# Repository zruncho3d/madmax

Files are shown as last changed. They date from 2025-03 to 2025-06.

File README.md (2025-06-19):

## MadMax - the crazy-simple toolchanger *conversion* for your CoreXY printer

Enable multi-material printing *on the printer you already own* - with low cost, low effort, low filament waste, and fast multi-material switching.
<br><br>

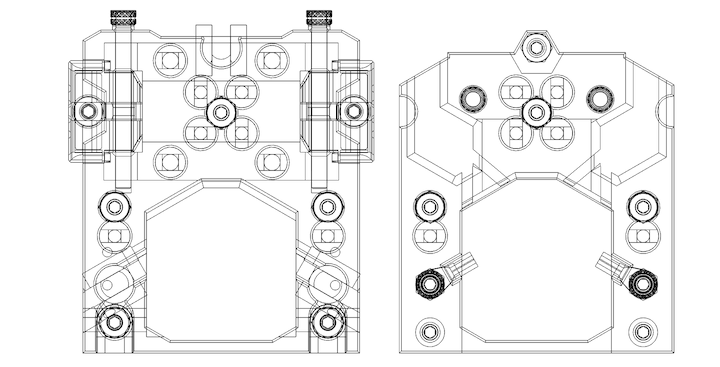
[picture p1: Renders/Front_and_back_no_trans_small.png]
 |  | gif | gif |
| --- | --- | --- |
| Solid Core<br>new plate + carriage design using Maxwell coupling | Fast Toolchanging<br>(`Yell`'s E3-to-Trident with AntHeads)  | Quality Printing<br> (`Andrewmcgr`'s VT 350 with A4Ts) |

<br><br>
**MadMax is currently in active beta**, with over 12+ completed builds doing two-head printing:
<br><br>

| Printer | Image | Sample | Description |
| --- | ---- | ---- | ---- |
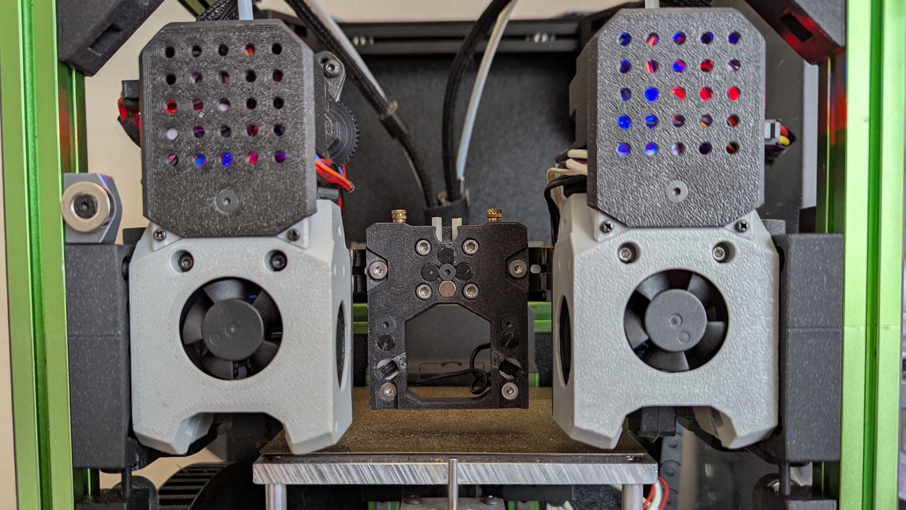
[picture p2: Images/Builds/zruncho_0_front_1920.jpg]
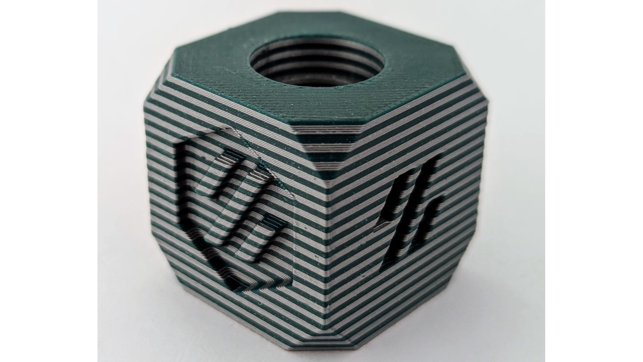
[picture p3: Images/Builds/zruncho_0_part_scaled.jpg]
| Zruncho's T0 120 (MM.000)|  |   | T0+B0, Vampire Bat, Nudge, custom rear-shift bed parts, OmniBrick heads, PapLite belt extruders, docks + brushes/blockers by Zruncho.|
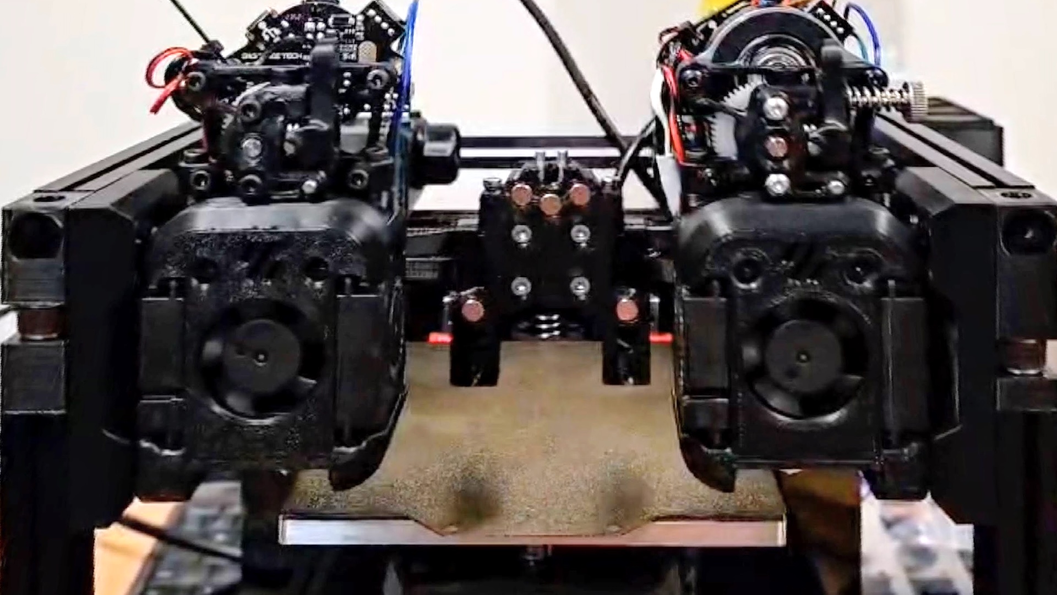
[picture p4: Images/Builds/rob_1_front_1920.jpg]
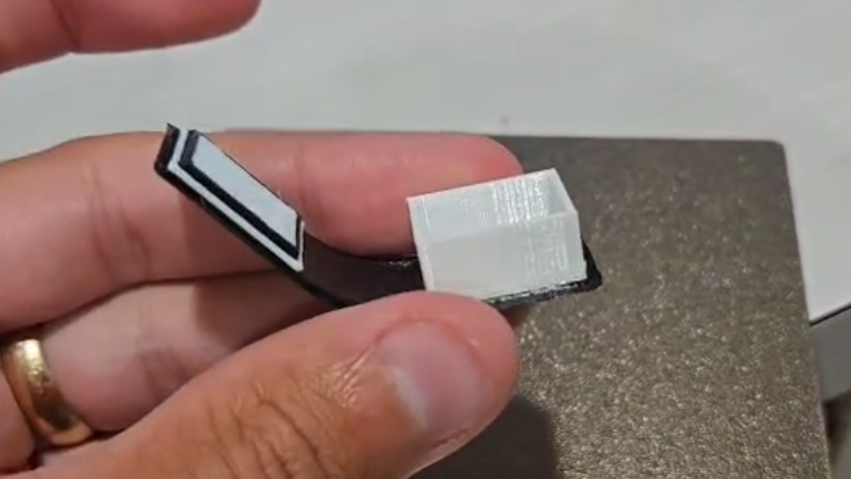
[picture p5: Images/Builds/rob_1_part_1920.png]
| Rob's V0 120 (MM.001) |  |  | Voron Zero, Vampire Bat, DragonBricks, V0 docks by Rob, Custom K1 extruders by Rob.|
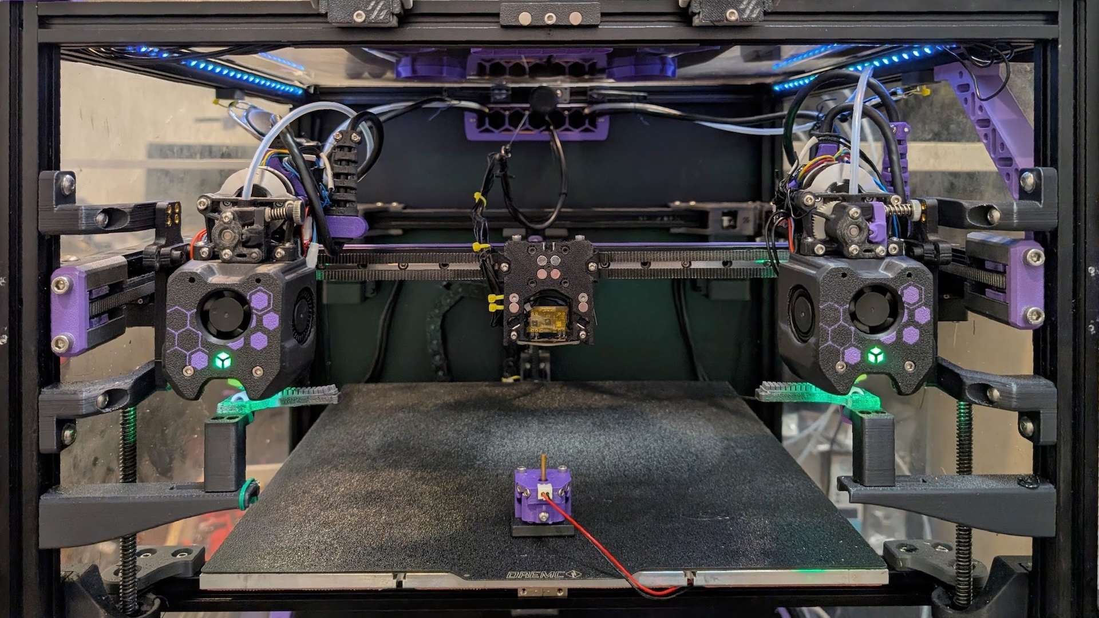
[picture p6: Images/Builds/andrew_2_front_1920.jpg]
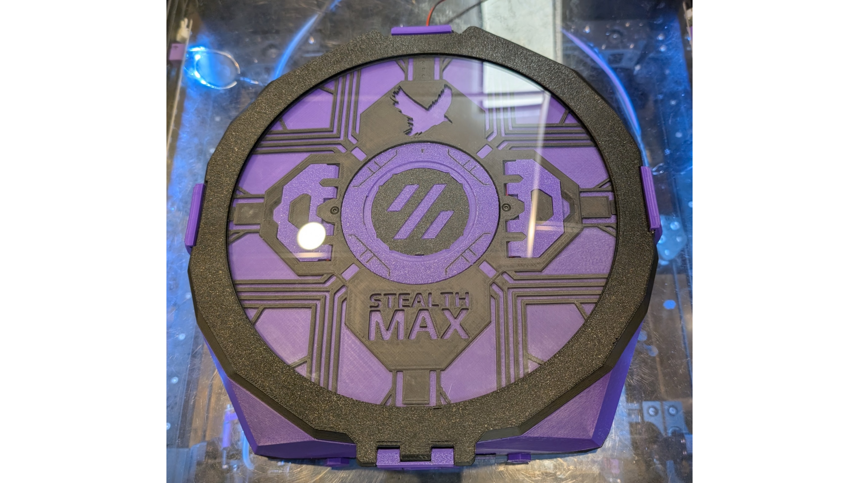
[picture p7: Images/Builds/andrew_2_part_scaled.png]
| andrewmcgr's VT 350 (MM.002) |  |  | Trident 350, A4Ts, Sherpa Minis, TMC 4671 closed-loop servo XY drives, BFI, Cartographer. Docks, brushes, carriage, plate by Andrew.|
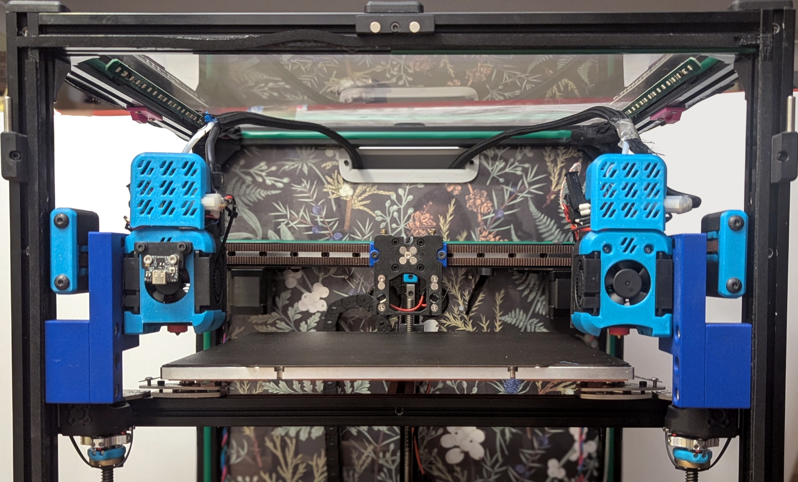
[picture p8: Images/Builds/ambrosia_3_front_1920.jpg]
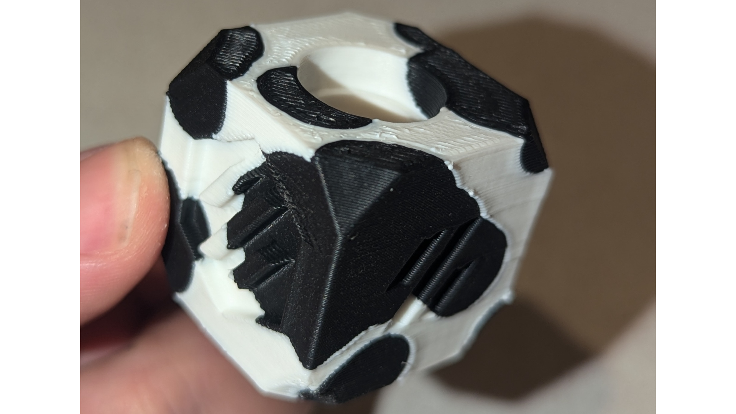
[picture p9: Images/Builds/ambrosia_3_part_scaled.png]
| Ambrosia's Metal VT (MM.003) |  |  | Metal Trident with DragonBricks, Trident stalagmite docks by Ambrosia, as seen on [Canuck Creator](https://www.youtube.com/watch?v=dB9FqNF6or0&t=164s)! |
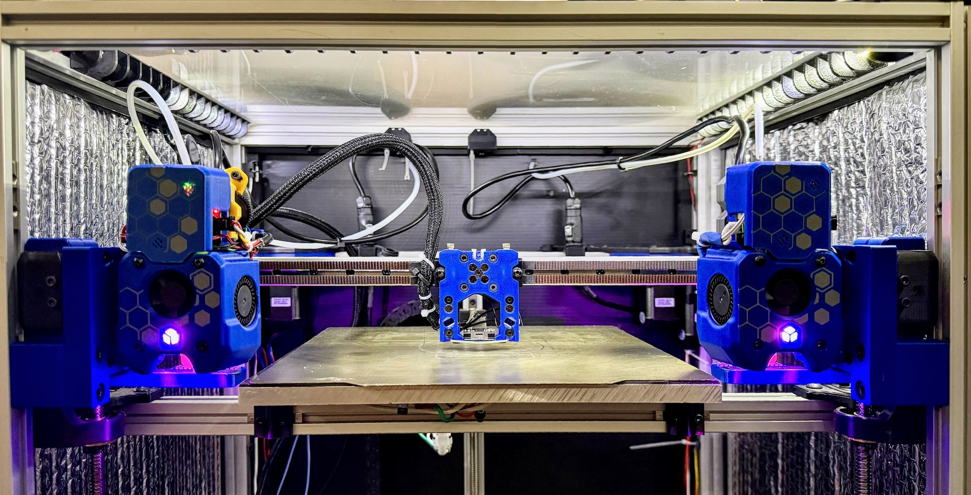
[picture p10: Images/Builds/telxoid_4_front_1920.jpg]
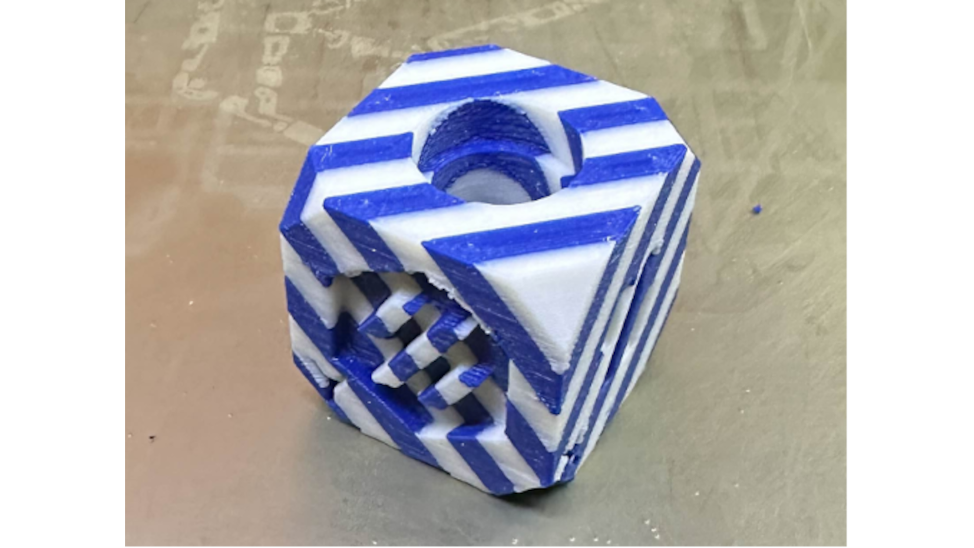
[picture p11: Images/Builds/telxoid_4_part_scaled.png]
| Telxoid's Tridex 250 (350 wide) (MM.004) |   |  | Tridex, A4TBrick, PapLite belt extruders, docks + brushes/blockers by Telxoid.  Running y-assist CoreXY!
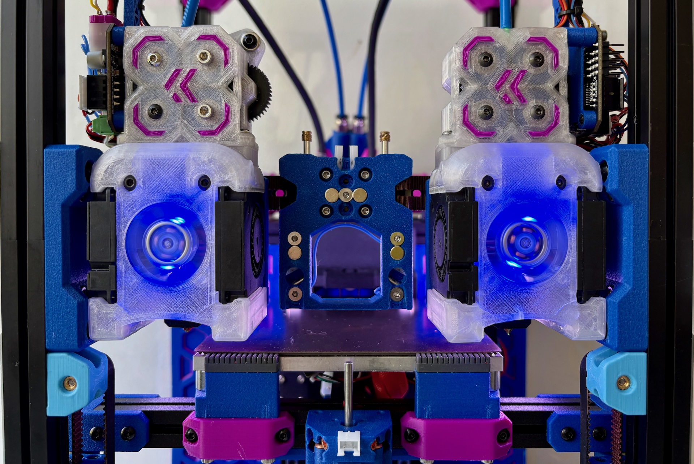
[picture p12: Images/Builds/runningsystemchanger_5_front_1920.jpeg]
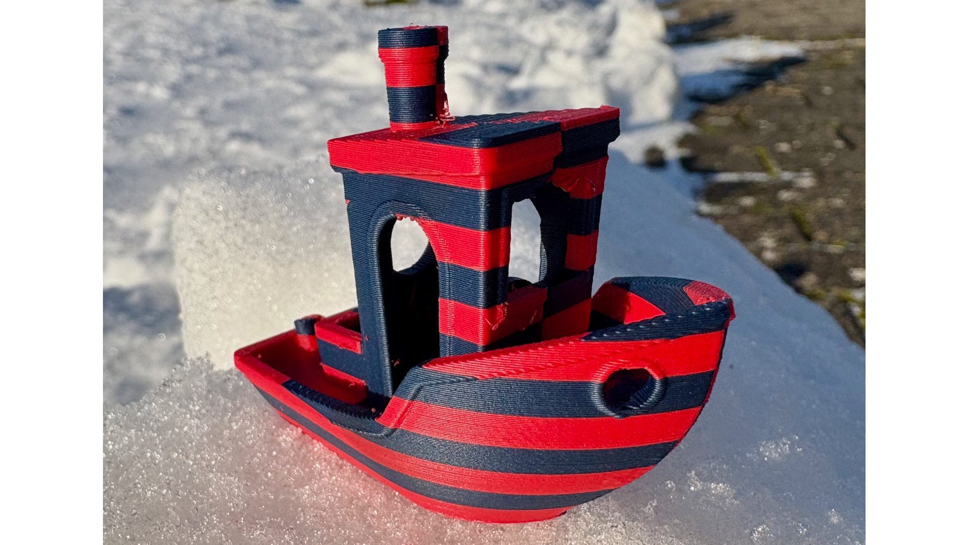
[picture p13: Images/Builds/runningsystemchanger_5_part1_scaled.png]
| Max's HX0 120 (MM.005) |  |  | HX0+B0, VB, DBs, custom PapLite Slim mount, side-mount TH board, Y-shift HammerHead bed by Max.|
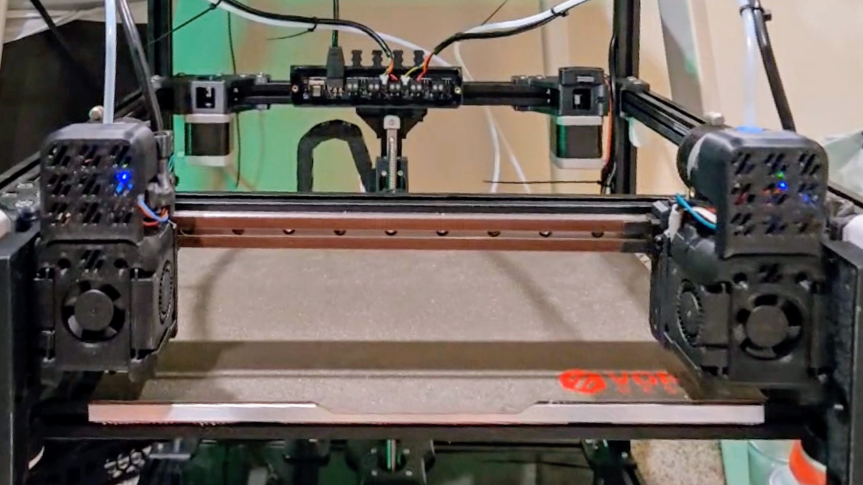
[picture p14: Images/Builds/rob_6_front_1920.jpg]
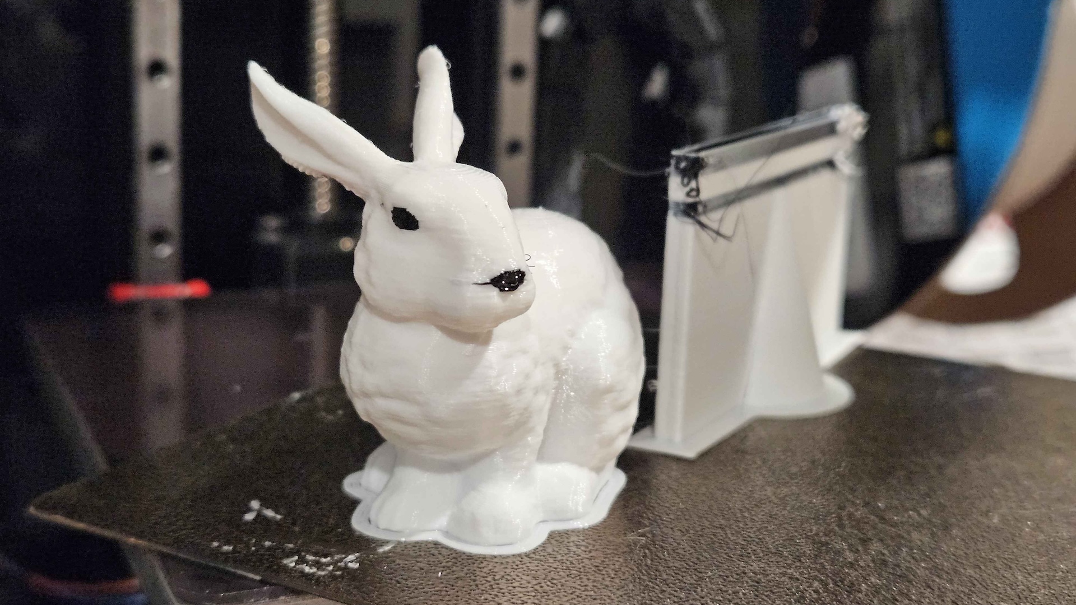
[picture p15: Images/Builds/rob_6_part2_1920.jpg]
| Rob's VT (MM.006) |  |  | RapidBrick heads by Rob, Trident stalagmite docks by Ambrosia.|
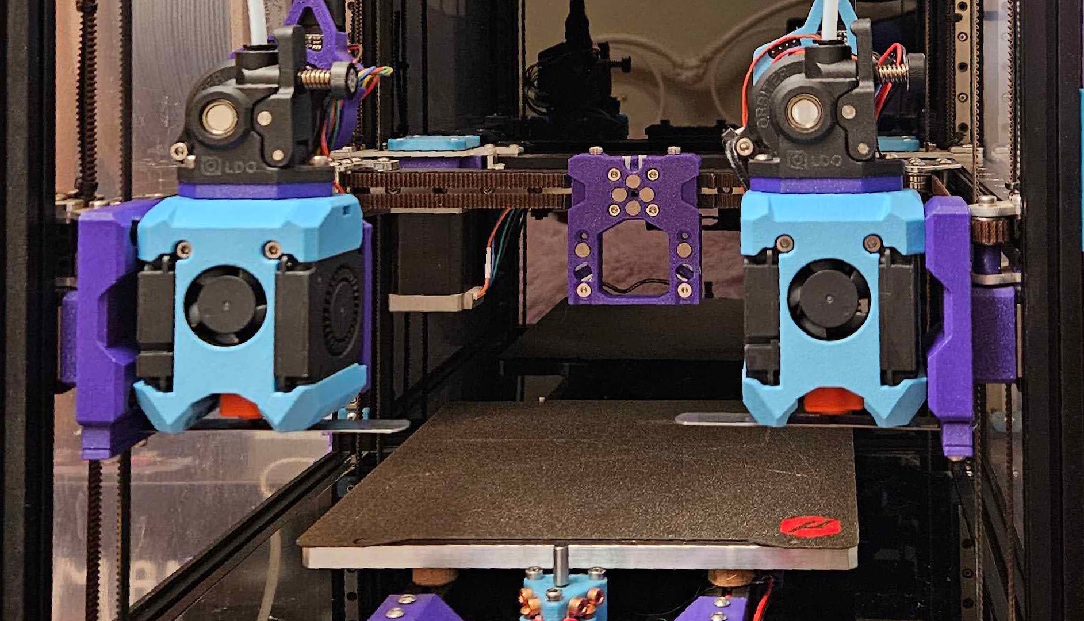
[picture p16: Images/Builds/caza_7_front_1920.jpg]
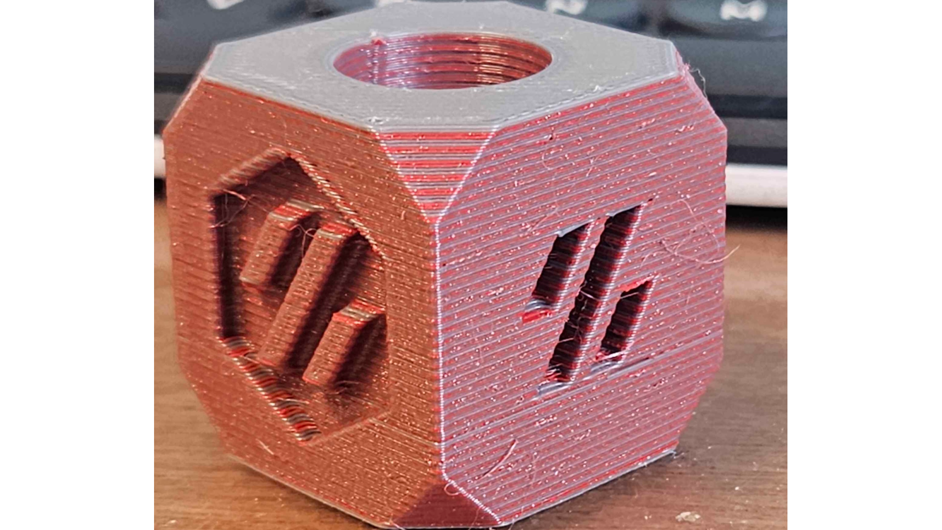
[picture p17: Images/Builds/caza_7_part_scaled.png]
| Caza's Metal Micron (MM.007) |  |   |  Yavoth heads by Caza, Orbiter extruders, Micron Docks by Caza.
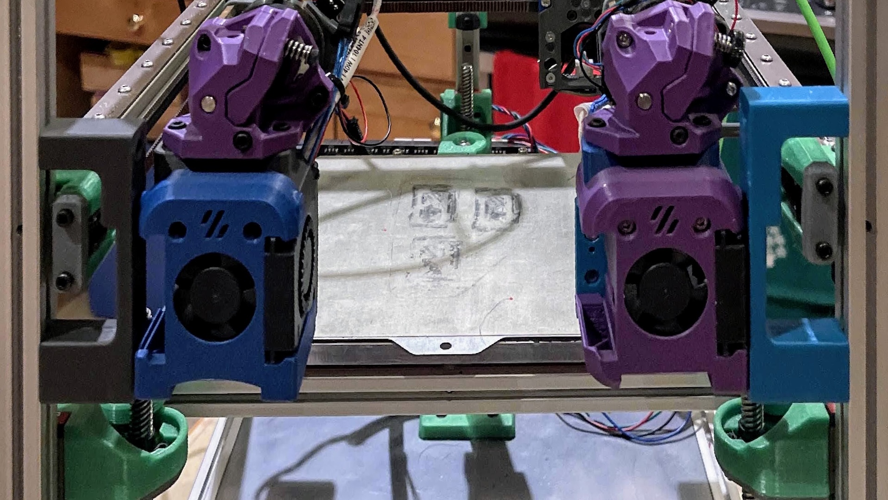
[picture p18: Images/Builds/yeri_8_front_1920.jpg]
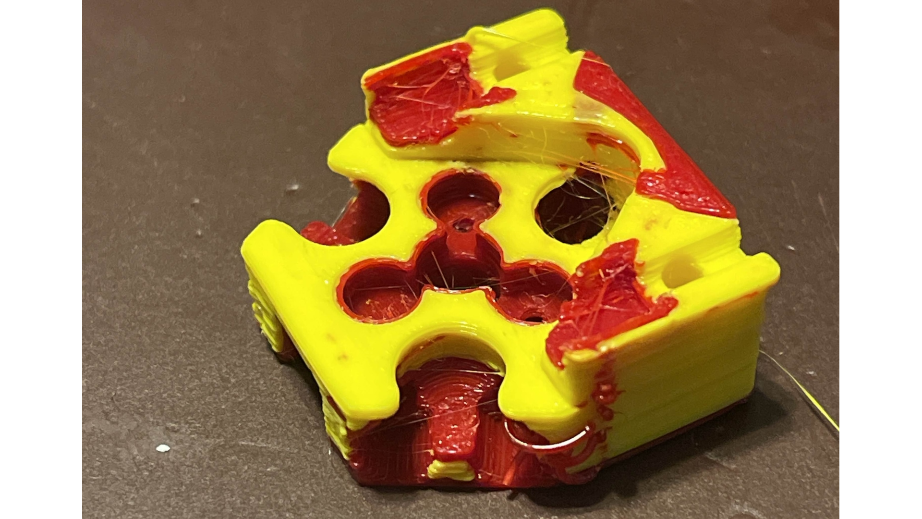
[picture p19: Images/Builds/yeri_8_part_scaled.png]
| Yeri's SF 160 (MM.008) |  |  | Salad Fork wraparound docks by Yeri, DragonBrick heads by Rob, G2Z extruders.|
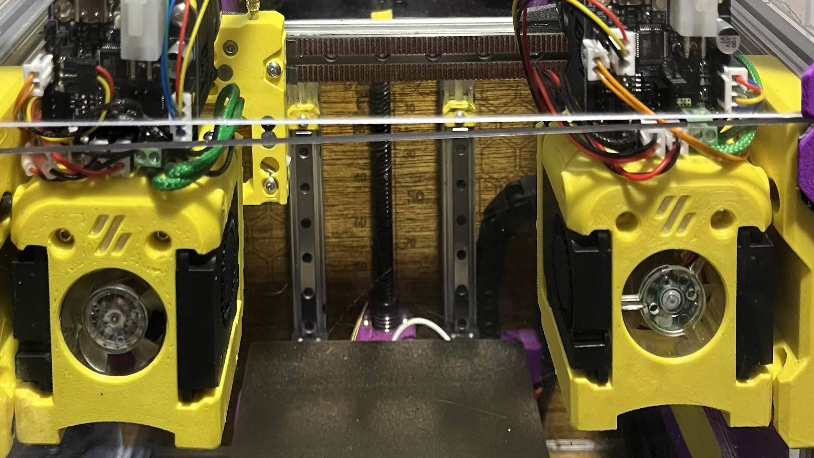
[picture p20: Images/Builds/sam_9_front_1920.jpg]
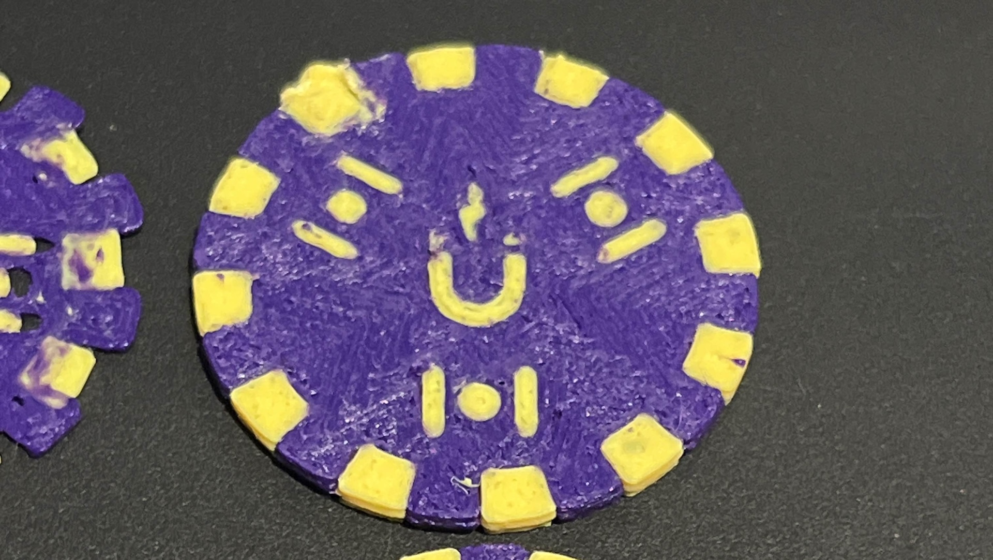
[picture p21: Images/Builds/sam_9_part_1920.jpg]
| Sam's V0.2 120mm +30X (MM.009) |  |  | Docks by Rob, DragonBrick heads by Rob, LGX Lite extruders, customized extra-wide Vampire Bat gantry by Sam.|
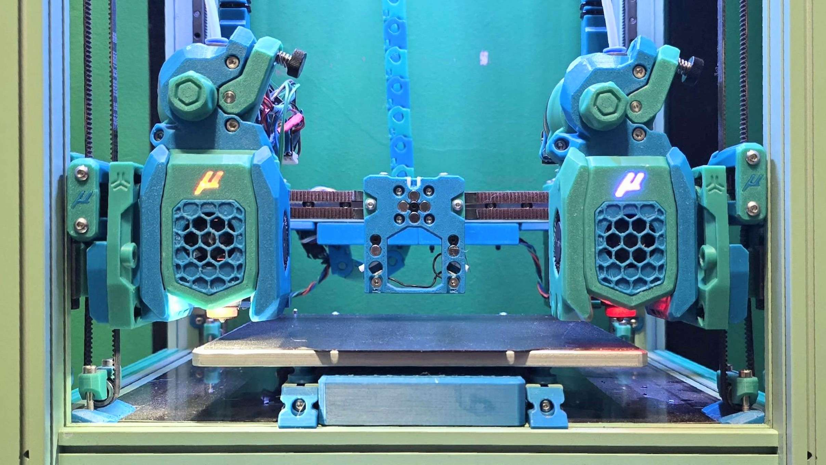
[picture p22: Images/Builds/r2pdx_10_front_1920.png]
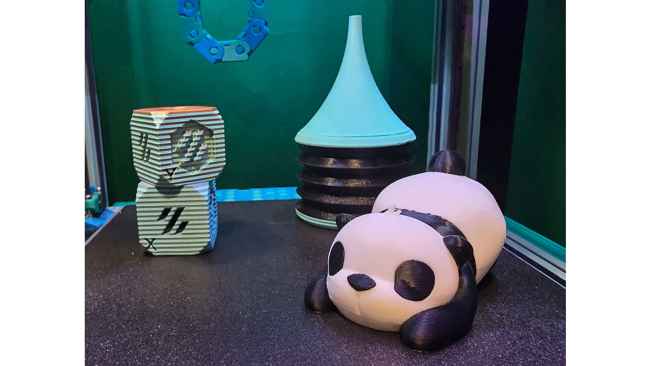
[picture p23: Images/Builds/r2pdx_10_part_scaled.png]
| r2pdx's Micron 180 (MM.010) |  |  | Micron 180r1, AntHeads with modified ducts and WWG2 extruders, Nudge, gantry-mounted docks by r2pdx (also tested frame mounted docks).|
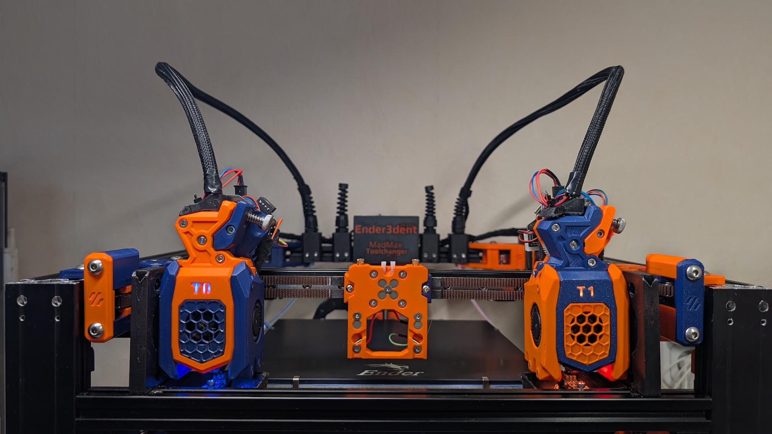
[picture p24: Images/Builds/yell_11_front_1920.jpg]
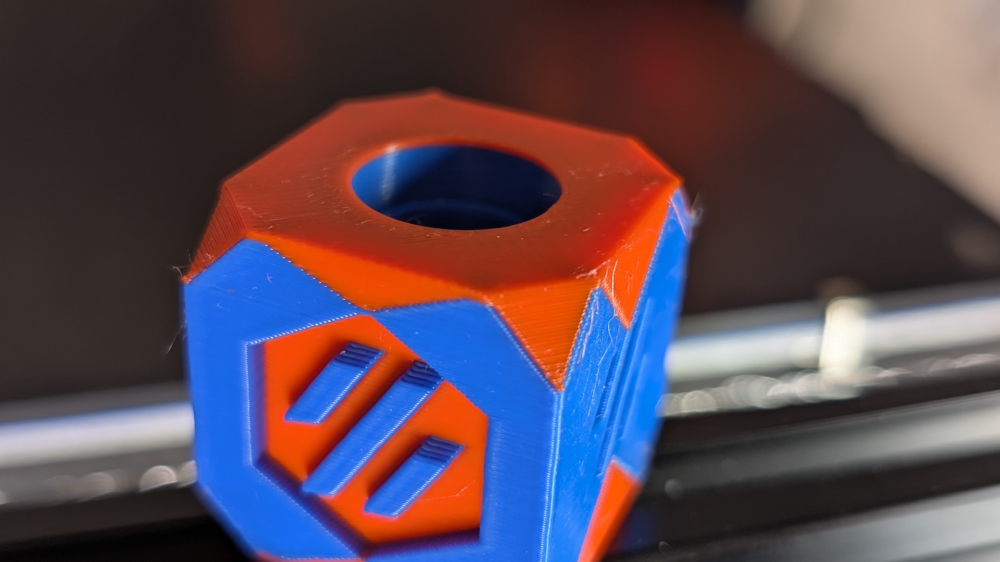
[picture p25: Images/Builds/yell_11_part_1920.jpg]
| Yell's [Ender3-to-Trident-conversion](https://github.com/yell3D/Ender3dent) (MM.011) |  | | E3dent, AntHeads, GBB15 gantry board/CAN bridge; docks, bucket & brush by Yell. Crossbar for >= 2 heads!|
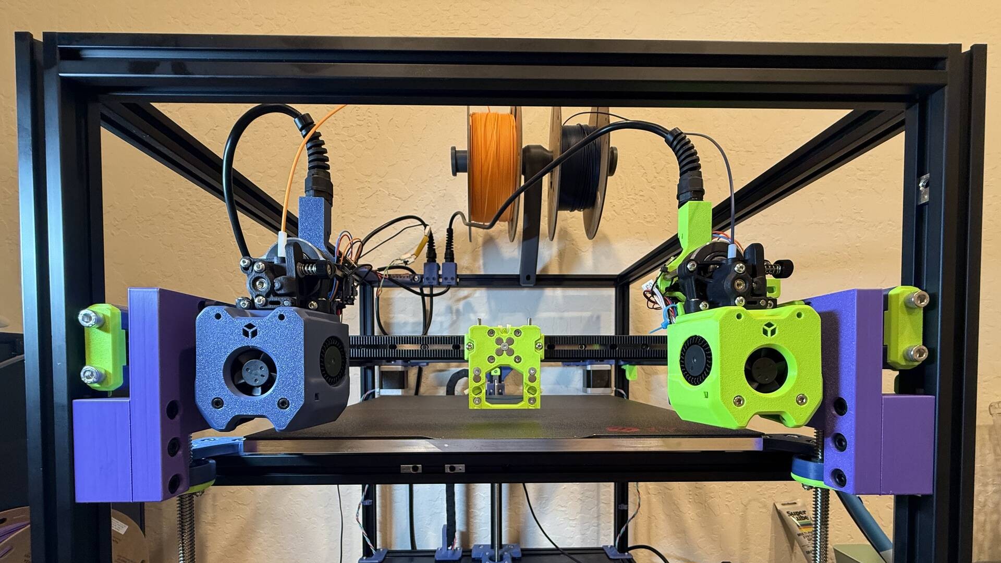
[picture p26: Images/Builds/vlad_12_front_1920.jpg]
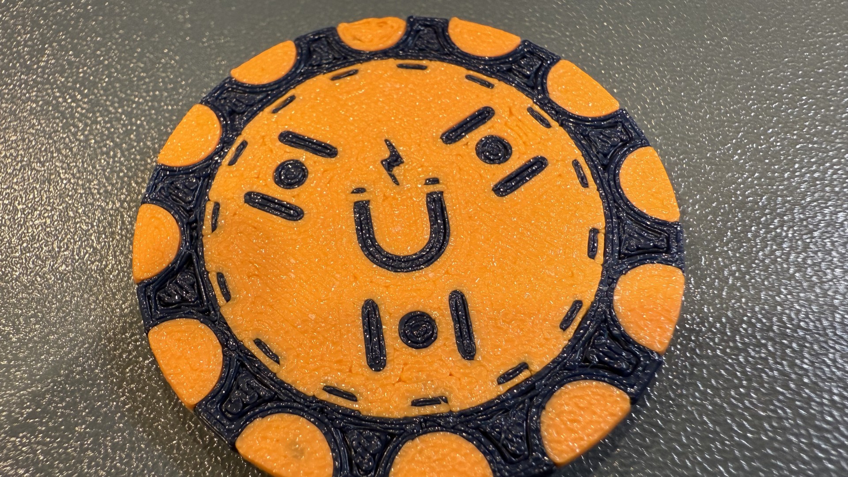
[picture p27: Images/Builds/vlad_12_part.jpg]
| Vlad's 300-ish Trident (MM.012) |  | | A4T, Sherpa Mini, Andrew's add-on brackets, extended Ambrosia's docks. Eddy current XY toolhead alignment! |

Learn more from videos:
* [Canuck Creator interviews Ambrosia](https://www.youtube.com/watch?v=dB9FqNF6or0&t=164s) - with a MadMax Trident
* [Speedclips.... they're real, and they're spectacular](https://www.youtube.com/watch?v=UsWV_GbRdjc)
* Core Build (coming later)
* Selecting a Toolhead (coming later)

**This is an advanced mod**: you must be comfortable with modifying Klipper configs and debugging related error messages, and potentially, doing small CAD mods to fit your printer.

**This project is in beta**: parts are well-tested/well-trusted and docs are complete, but parts may change in the future.

Earlier in a project is where your efforts will have the highest impact, so now's the time to jump onboard!

## New part concepts, all easily sourced

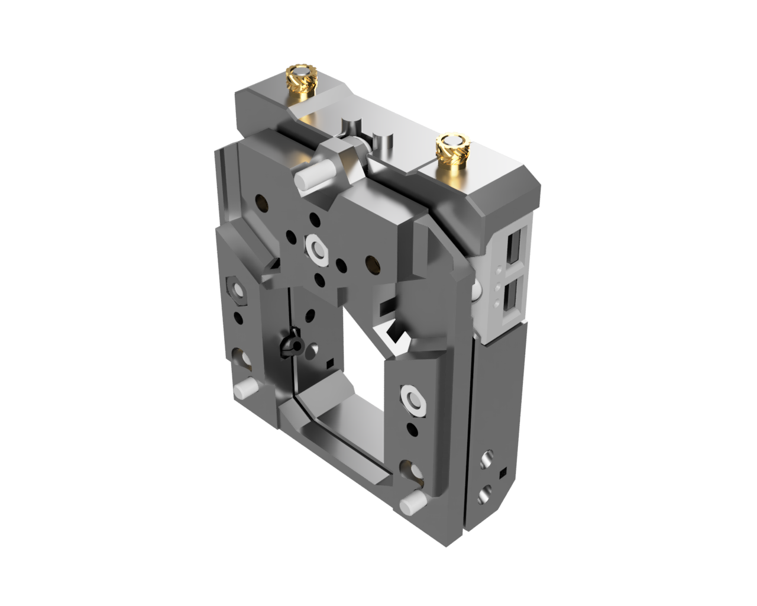
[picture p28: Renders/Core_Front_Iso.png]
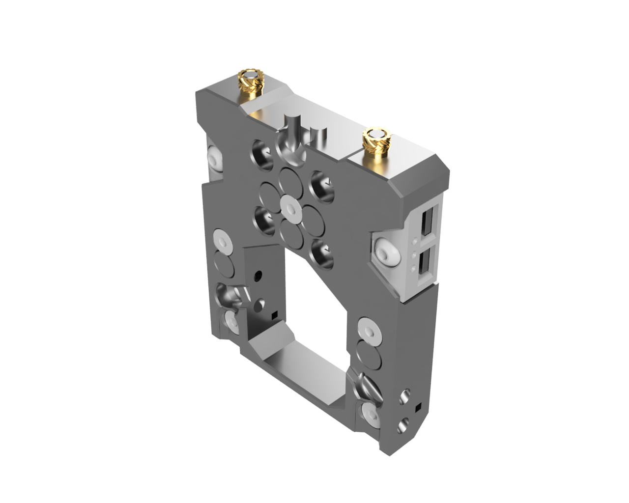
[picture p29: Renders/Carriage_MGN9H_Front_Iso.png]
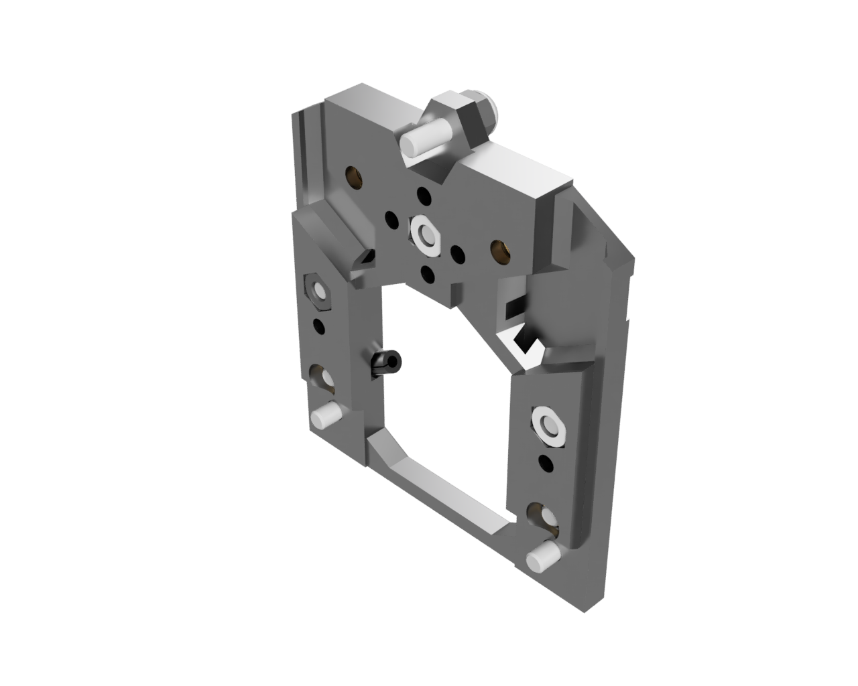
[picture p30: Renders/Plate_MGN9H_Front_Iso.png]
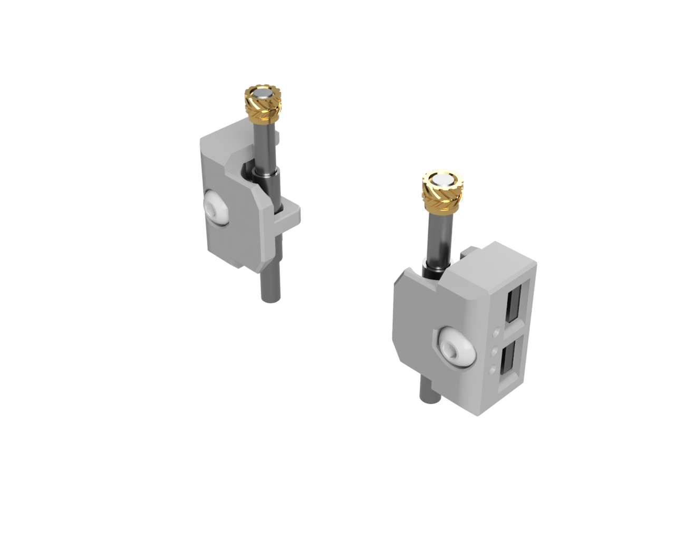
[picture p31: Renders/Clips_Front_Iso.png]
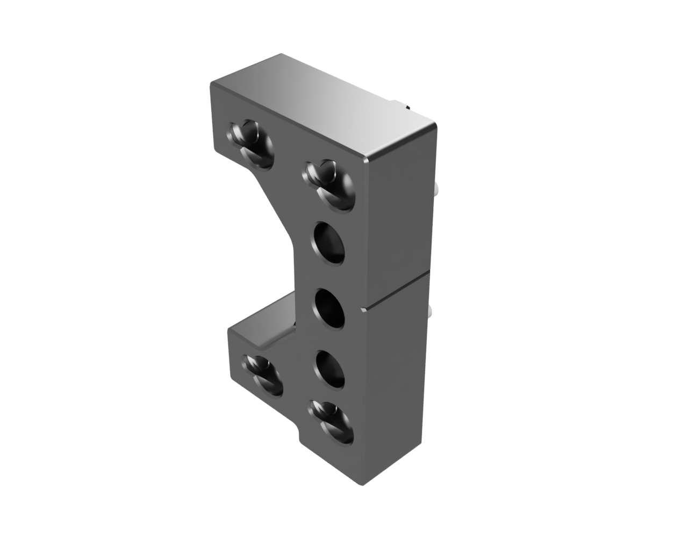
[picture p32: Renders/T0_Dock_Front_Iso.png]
|  |  |  |  |  |
| --- | --- | --- | --- | --- |
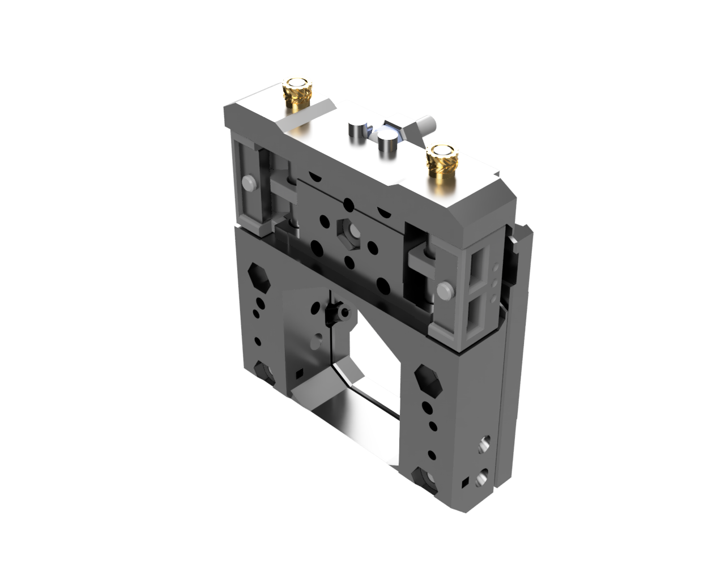
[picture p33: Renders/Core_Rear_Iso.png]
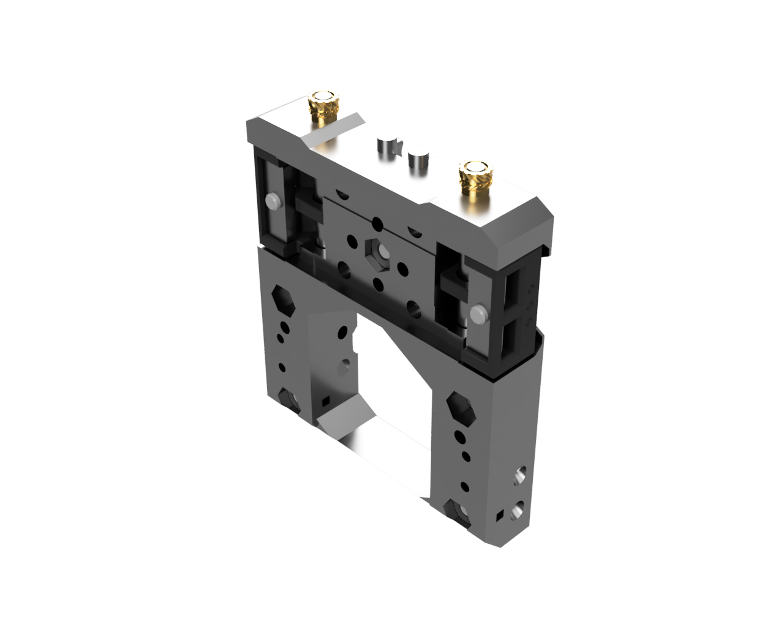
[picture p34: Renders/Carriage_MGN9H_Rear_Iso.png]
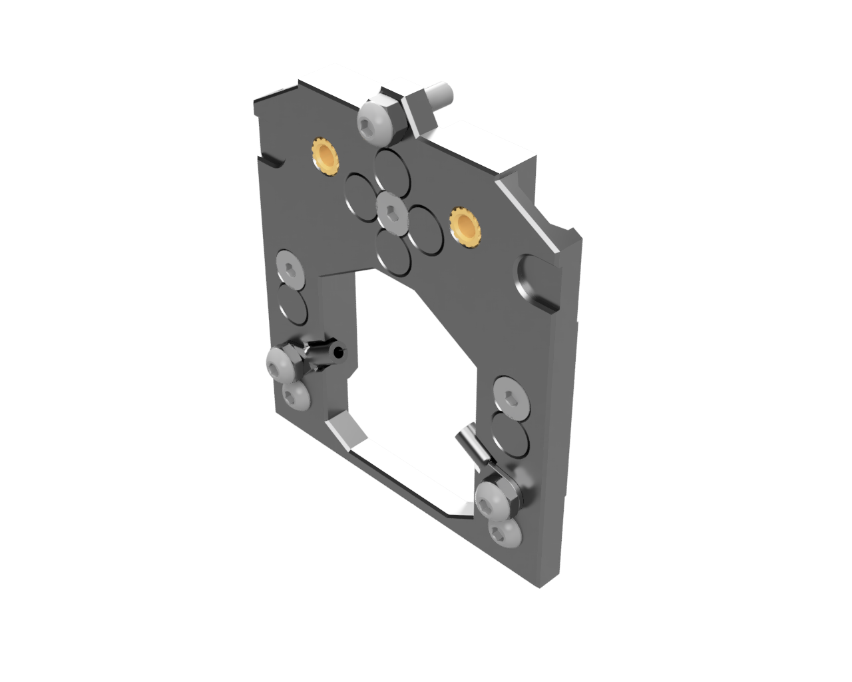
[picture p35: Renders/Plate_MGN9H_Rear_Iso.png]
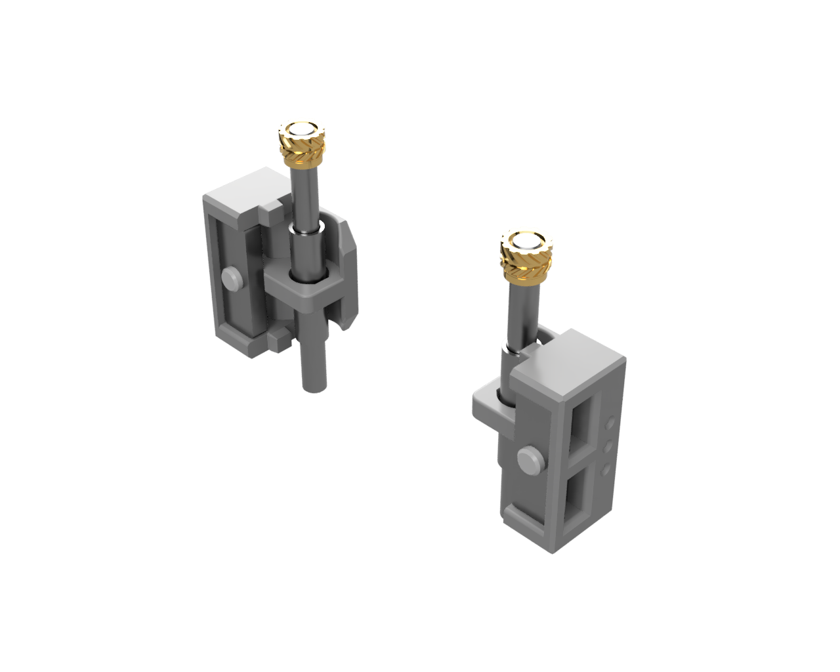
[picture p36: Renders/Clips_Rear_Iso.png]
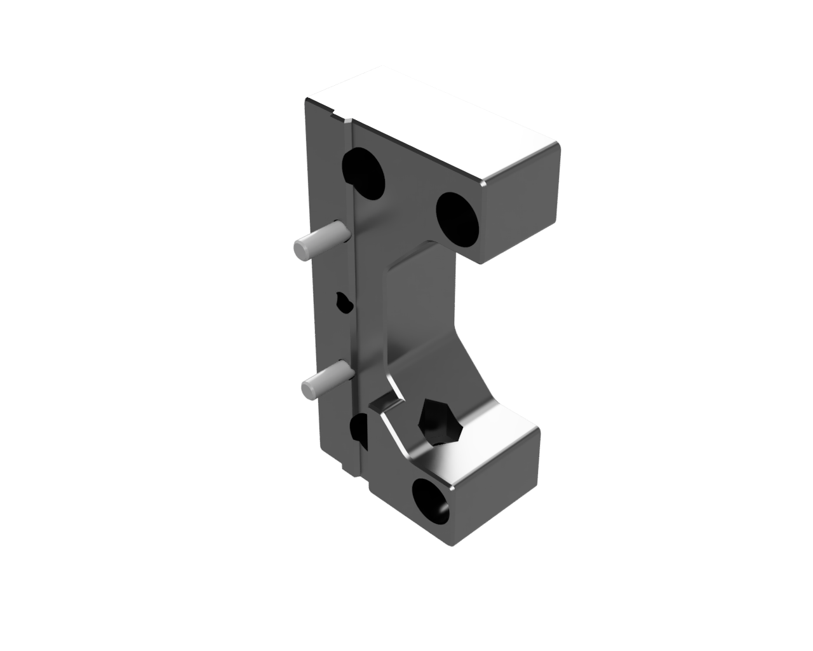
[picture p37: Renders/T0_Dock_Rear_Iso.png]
|  |  |  |  |  |
| Core<br>(Carriage + Plate + Clips) | Carriage | Plate | Clips | Sample Dock (V0/T0) |

A combination of new parts makes it possible:
* **Core:** A new “pins and screws” magnetic [Maxwell](https://en.wikipedia.org/wiki/Kinematic_coupling) coupling enables head attach/detach, head detection, AND probing.  
  * Yes, you heard that correctly!   The core carriage+plate mechanism _is_ the probe, if you want.  The Maxwell coupling is engineered to slide in place with low friction, enabling high-quality probing up there with Tap and Boop, but lighter, lower-cost, and with more stable motion.  Here's a sample probe run:
  `probe accuracy results: ... range 0.002031,... standard deviation 0.000548`.  Not bad!  In fact, you can use the core on non-toolchangers too, as a Tap/Boop replacement.
* **Clips:** The new SpeedClips belt clips are the fastest belt attachment mechanism in the west, plus enable repeatable tensioning.
* **Docks:** The docks use simple keyslots and magnets, with the toolhead modified to add ferrous flat-head screws.  It's all light, low-cost, small, and simple.

All parts use reasonably-sourceable components, like pins, screws, and magnets. It’s a more straightforward mod than you might think.

So, what's the catch?
* Some lost XY build area, when printing with two heads. **Space loss is inherent to all toolchangers**, but for single-head prints, you can detach the second head in seconds, to restore nearly the full original build volume.
* No positive lock on the toolhead - only a magnetic hold.  In practice, this works fine, and means that no complex locking mechanism or motors are needed, plus it enables the probing method.  It's safe; should the head detach for any reason, the firmware immediately safes the printer, just like with any other fault.
* Some printers and toolheads will need some CAD work before they're print-and-play.
* The lower two BHCS screws on the coupling may wear with time and need replacement for reliable probing.  
* No builds seen beyond two heads, yet.

That’s about it.  Read on to learn what a MadMax can do.

## Enable serious new capabilities

This mod is for those who want a more capable printer.  The surprise is that you can enable *many* new capabilities, with only about $100, one night of printing, one night of building, and one night of configuration and tuning.

| Use case | Multiple colors  | Multiple materials | Full-contact supports | Tap/Boop replacement |
| --- | --- | --- | --- | --- |
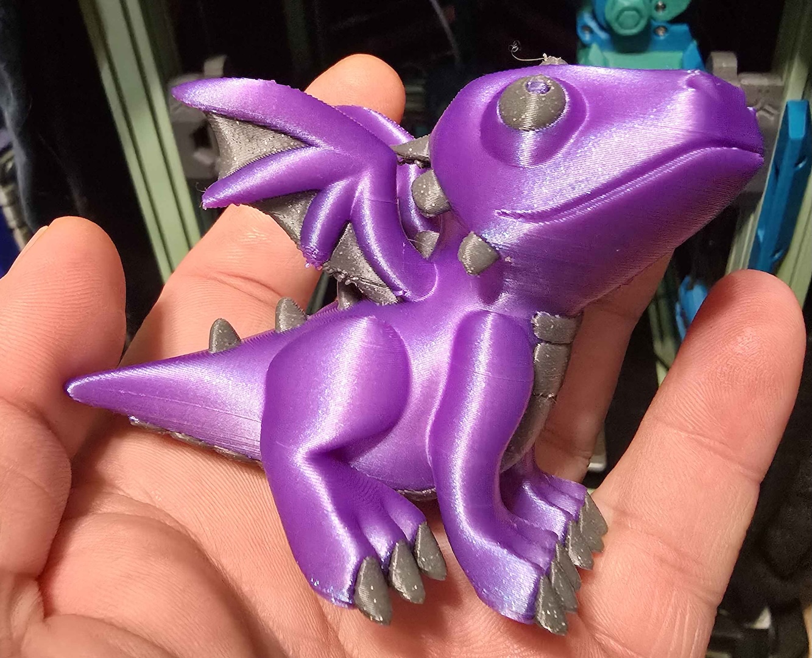
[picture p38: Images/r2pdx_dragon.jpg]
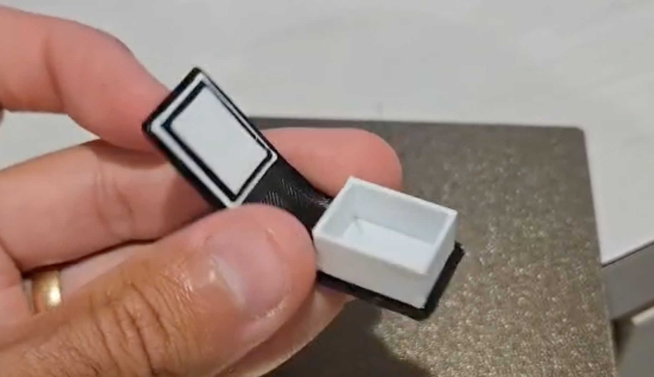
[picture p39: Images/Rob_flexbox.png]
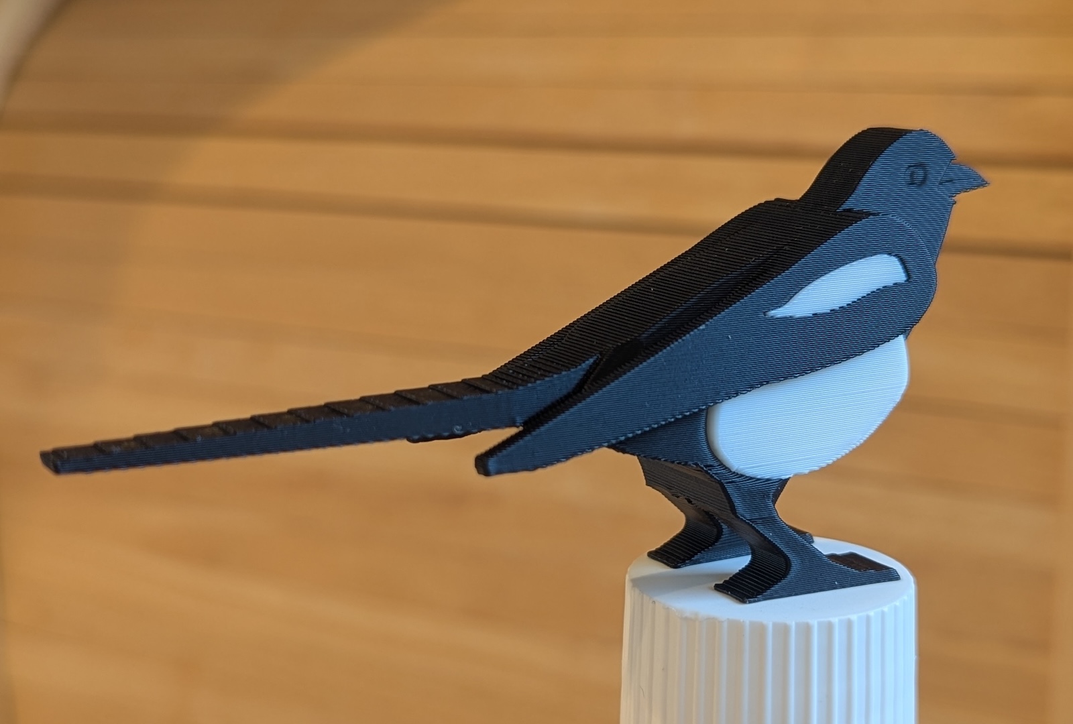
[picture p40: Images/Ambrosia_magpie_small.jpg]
| Example(s) |  |   |   |  |
| Notes | Dragon printed by r2pdx, on MM.010 | Flexible box printed by Rob on MM.001 | Magpie printed by Ambrosia on MM.003  | Core weighs ~50g  |
| Benefits |  No adhesion issues/bleed vs MMU, vastly reduced waste and delay, can use TPU | No adhesion/mixing issues vs MMU, vastly reduced waste and delay | Clean support interfaces, with no mixing issues vs MMU | Lighter weight and better IS results, plus detach head for easy maintenance |

Unlike toolchanger designs that require up/down docking motion, MadMax supports static-gantry printers (like Voron Trident), *without* the added cost/complexity of a [liftbar](https://github.com/viesturz/tapchanger/blob/main/Dock/Liftbar/Liftbar.md).  

XY-only toolchanges are lightning-fast, which can speed up overall print time, improve print quality, simplify print tuning, and reduce priming waste.

## An entire toolchanger ecosystem

MadMax is more than just the core and dock interfaces; already, **it is an entire toolchanger ecosystem** covering many common [Voron](https://vorondesign.com/) and [Printers for Ants](https://3dprintersforants.com/) printers, plus many open-source toolheads and extruders.  

| Carriages | Belt Configs | Toolheads (core only) | Toolheads (to docks) | Printers |
| --- | --- | --- | --- | --- |
| 2 | 3 | 6+ | 7+ | Lots |
| MGN9H<br>MGN12H | 6mm w/3mm sep<br>6mm w/4mm sep<br>9mm w/4mm sep| MiniSB<br>OmniBurner<br>DragonBurner<br>RapidBurner<br>A4T<br>XOL | DragonBrick<br>RapidBrick<br>AntHead<br>A4T<br>A4TBrick<br>OmniBrick<br>XOL<br> |  Voron Trident<br>Voron Zero<br>Micron<br>Salad Fork<br>Tri-Zero<br>Pandora's Box<br>[E3-to-Trident-conversion](https://github.com/yell3D/Ender3dent) |

If you don’t see your printer in the list below, adding it tends to be straightforward.

The main requirement is a front-facing MGN9H or MGN12H linear rail and XY head motion, so bed slingers and rod riders are out.

A subset of the supported heads: A4T, AntHead, OmniBrick, DragonBrick:

|  |  |
| --- | --- |

Note that MGN9H plates have a diamond of magnets, whereas MGN12H plates have a square of magnets.

## Easy to print, build, and configure

All parts are easy and fast to print, with no large overhangs, no large bridges, and supports included.

Here's a full plate for the MadMax core parts for a conversion:



To this plate, you would add printer-specific toolheads and docks.

The entire conversion can be done in an evening, as covered by instructional videos, and no individual steps are hard.

Sample Klipper configuration is available in this repo, for [Viesturz' klipper-toolchanger](https://github.com/viesturz/klipper-toolchanger), but [TypQxQ's KTC2](https://github.com/TypQxQ/KTC) and [Bikin Toolchanger](https://github.com/Bikin-Creative/Lineux-Toolchanger/tree/main/Klipper) are also potential choices.

Calibration is fully automated (using [Nudge](https://github.com/zruncho3d/nudge)), can run on every print (using [r2pdx's macros](https://github.com/joseph-greiner/klipper_tc_automatic_offset_calibration)), and includes head crash detection for safety.

Automatic offset calibration is a big deal for the overall experience of a toolchanger, because it removes the main source of pain relative to automated filament changers.  You can change hotends or adjust the mount - things which can affect offset calibration - and there’s no work to do, because calibration is automatic.  Plus, any differences in offsets due to temperature or changes to the positions of the heads or the frame are automatically accounted for, by probing at the operating temp.

### Key features
* Support for a wide range of printers and toolheads, including static-gantry printers
* Fast toolhead changing for faster, better multi-extruder prints
* Bonus Maxwell-coupling-driven nozzle probing
* Toolhead failure detection without extra parts
* Bonus pragmatic features:
 * Pinned carriage enables reproducible retensioning
 * Fully reversible conversion process
 * Documented and simplified steps for toolchanger setup with Klipper
 * Reliable: no glue, no servos to fail, no liftbar parts to fail

## What's here?
- #### [Getting Started](GETTING_STARTED.md) - select a printer, toolhead, and extruder, amongst choices
- #### [BOM](BOM.md) - parts to procure
- #### [Instructions](INSTRUCTIONS.md) - print and build steps
- #### [Configuration](CONFIGURATION.md) - Klipper config and calibration
- #### [Story](STORY.md) - how and why this project came to be
- #### [Design](DESIGN.md) - notes on design choices; especially useful for doing ports
- #### [FAQ](FAQ.md) - covers questions you may have; worth a skim
- #### [Troubleshooting](TROUBLESHOOTING.md) - steps to diagnose the most-common errors

## Get Support

We now have a channel, `#madmax-toolchanger`, on the DoomCube Discord, in the misc-3dp area.  For now, this is the official home for all discussions and dev updates.  Go there!

[DoomCube Discord](https://discord.gg/doomcube)

## Support the creator
Like what you see?  [Buy me a coffee](https://ko-fi.com/zruncho3d) to show the love and enable future mods and content - stuff like [F0](https://github.com/zruncho3d/f-zero), [T0](https://github.com/zruncho3d/tri-zero), [B0](https://github.com/zruncho3d/boxzero), [X0](https://github.com/zruncho3d/double-dragon), [D0](https://github.com/zruncho3d/DuelingZero), [DX](https://github.com/zruncho3d/DuelingX), [ZeroPanels](https://github.com/zruncho3d/ZeroPanels), [ZeroClick](https://github.com/zruncho3d/zeroclick), [NoDropNuts](https://github.com/zruncho3d/f-zero/tree/main/STLs/NoDropNuts), [Poke](https://github.com/zruncho3d/poke), [Nudge](https://github.com/zruncho3d/nudge), [Vampire Bat](https://github.com/zruncho3d/vampire_bat), and more.

 :heart: *-Zruncho*

This one took a lot of prototypes and time.  Here's a partial set, which shows evolution from toys at the top, to little mods to try out the idea (green/gray near top left), to a range of increasingly reliable and solid carrriages and plates.



## Updates and timeline

* 2025-02-15 Started the GitHub conversion process
* 2024-11-04 Beta-3 files shared: new CAD, stiffer, better airflow, washers for wires, lots more
* 2024-09-12 Beta-2 files shared: MGN12 support, adds 120 degree option, better probe wiring, locking screws for magnets, nuts/screws instead of set screws ... lots of changes
* 2024-08-01 Spinoff: automatic magnet tester built - tests magnet strength, probe force, and more
* 2024-06-08 Proper closed beta program launches, with beta-1 files
* 2024-05-14 First two-extruder prints
* 2024-04-01 Spinoff: [Vampire Bat](https://github.com/zruncho3d/vampire_bat) release
* 2024-04-10 Spinoff: [Nudge](https://github.com/zruncho3d/nudge) release
* 2024-01-14 Spinoff: manual magnet tester
* 2023-12-10 Started collaborating on MadMax, as a front-mount TC
* 2023-09-02 First desk toys with Maxwell couplings, intended for a TC

## Credits

Thanks to all those who contributed to the beta program in some form, especially `caza` for a range of early testing, plus those who got all the way and contributed designs - `Rob`, `andrewmcgr`, `Ambrosia`, `Telxoid`, `Max`,  `Yeri`, `Sam`, `r2pdx`, 'Yell', 'Vlad', and more - plus those whose feedback provided encouragement - `Ankurv`, `hartk`, `clee`, `chirpy`, and more.

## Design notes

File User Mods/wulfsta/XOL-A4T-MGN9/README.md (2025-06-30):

## XOL MGN9 Plate

This is a simple modified version of the A4T plate from andrewmcgr to work with MGN9 carriages, since the magnet array is different.

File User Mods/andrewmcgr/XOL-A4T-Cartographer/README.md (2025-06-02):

The plate in this directory is compatible with toolheads designed for the XOL carriage. This includes A4T and XOL toolheads. It is compatible with standard MadMax carriages, and also with the version in this directory.

The carriage in this directory is for mounting Cartographer, Beacon, and mechanically compatible eddy-current probes on front-mounted MGN12 rails.

"Alternate Bracket" merges the dock bracket and toolhead board standoff from the plate. It's stiffer and results in cleaner tool changes, if it fits with your toolhead (works with A4T, not tested with XOL).

These parts are extensively tested on a Voron Trident 350.

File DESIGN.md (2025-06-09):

# Design

**This page tries to explain the design choices, especially the interesting ones.**

*Hopefully this section helps you understand why things are the way they are here, so you can better choose whether this project is right for you, and ideally learn a thing or two.*

No design is best, but a *good* design is one that understands what its goals and constraints are - then, achieves them under-budget, while delivering a good experience for the target audience.

**The audience for MadMax is NOT everyone.**  We're just not there yet.

It’s for leading edge, tip-of-the-spear types.

But, no single step is hard! If you can build and configure a Voron, you can do the MadMax steps too.

What we’ve tried to achieve here is *not* to fit every toolhead or printer, but to be the simplest on-ramp to adding a second toolhead possible, and fit most toolheads and printers with a single common design, so that ports happen from the community.

First, goals, requirements, metrics, and non-goals; without these explicitly defined, it can be harder to wrangle a project like this towards a release, even with one main developer.

## Goals
* Enable high-quality multi-toolhead printing, for as many printers as possible, at reasonable price

## Requirements

“Must be:” stuff:
* **Easily sourced**: ideally all COTS stuff; no rail grinding or cutting, minimal electronics per head, if possible
* **Safe**: crash detection is critical
* **Prints well**: with no ringing, and good resonance testing
* **Tolerant to misalignment**: ideally at least 0.5mm of alignment inaccuracy allowed in all dimensions, and ideally beyond
* **Performs**: ideally “weight neutral” or no more than 10% added head weight relative to other options
* **Versatile**: support a wide range of printers, with as much available travel as possible
* **Fast to convert**: minimize wiring changes needed; ideally, sub-1 hr

## Metrics

“Optimize for:” stuff:
* Cost: $100ish, or as low as possible, for the MadMax-specific parts and second head
* Fast toolchanges: sub-second (!) target, but 4s is plenty fast, in practice
* Minimize design work
  * Ideally, enable multiple unchanged or minimally changed toolheads from the V0 ecosystem.
* Ideally, conversion possible without having to reprint the first toolhead
* Ideally, enable multiple non-V0-ecosystem toolheads, too

## Not goals
* Any particular wiring layout; second umbilical for the shuttle is OK (for now) - maybe simplifies some startup firmware
* Support for full-size Voron toolheads - but, it happened anyway from Beta members :-)
* Initial support for more than two heads - but, nothing precludes this

## Choices

For the design that emerged.. below are some interesting parts/choices/features/attributes, and discussion around them.  Yes, it’s a lot.

#### No glue, no tape, no epoxy: mechanical fastening only
This isn’t trivial!   

You have to get the dimensions right to do press fits, like those used by the magnets, when every printer is slightly different.

We tried different sizes and magnet shapes, with a press fit, and a survey of builders.  How do you even do press fits when you want to use cylindrical magnets?  You test and find a happy medium.

In one early test in a hot chamber a magnet escaped, which motivated the magnet-retention screws, which use the tip of a screw to retain the magnet.

#### Reliable metal connections with no special parts
“Metal sandwich construction” is used for carriage wires, plus crimp terminals on the plate.

Originally we had set screws from the side, using formed threads.  It worked, but not for long, in a heated chamber.  Plastic deforms over time, loosening the connection, and the set screw could easily strip when tightened, too.  

Then we moved to screws squeezing wires, but the connections would get loose due to plastic creep.

Heat cycles cause expansion and contraction, and then the screws loosen, and the electrical connection becomes flaky.  I’d see this after just a few print cycles!  You could tighten the screws, but the flaky connection would come back eventually. It’s a fundamental deficiency; the metal expands more than the plastic, so inevitably it gets loose.

Now, layer lines are all aligned, and screws are in compression; you can’t split the layers by forming the threads.  There are no formed threads in the parts anymore, anyway.

What we have on the plate part (which sees the most heat) is solid: metal (ring terminal) touches metal (heatset).

The carriage has it a bit easier for now, heat-wise, and seems OK after an initial retightening.  This would be an area to improve.

#### Easy Printing w/no supports needed and no overhangs, just small bridges

The 4-layer bridges on the carriage are the most complex bridges I’ve ever done.  They're not hard to make; they just take time to ensure clean prints.  The plate, near the crimp cutouts, also has some complex bridge work.  Here's an example:

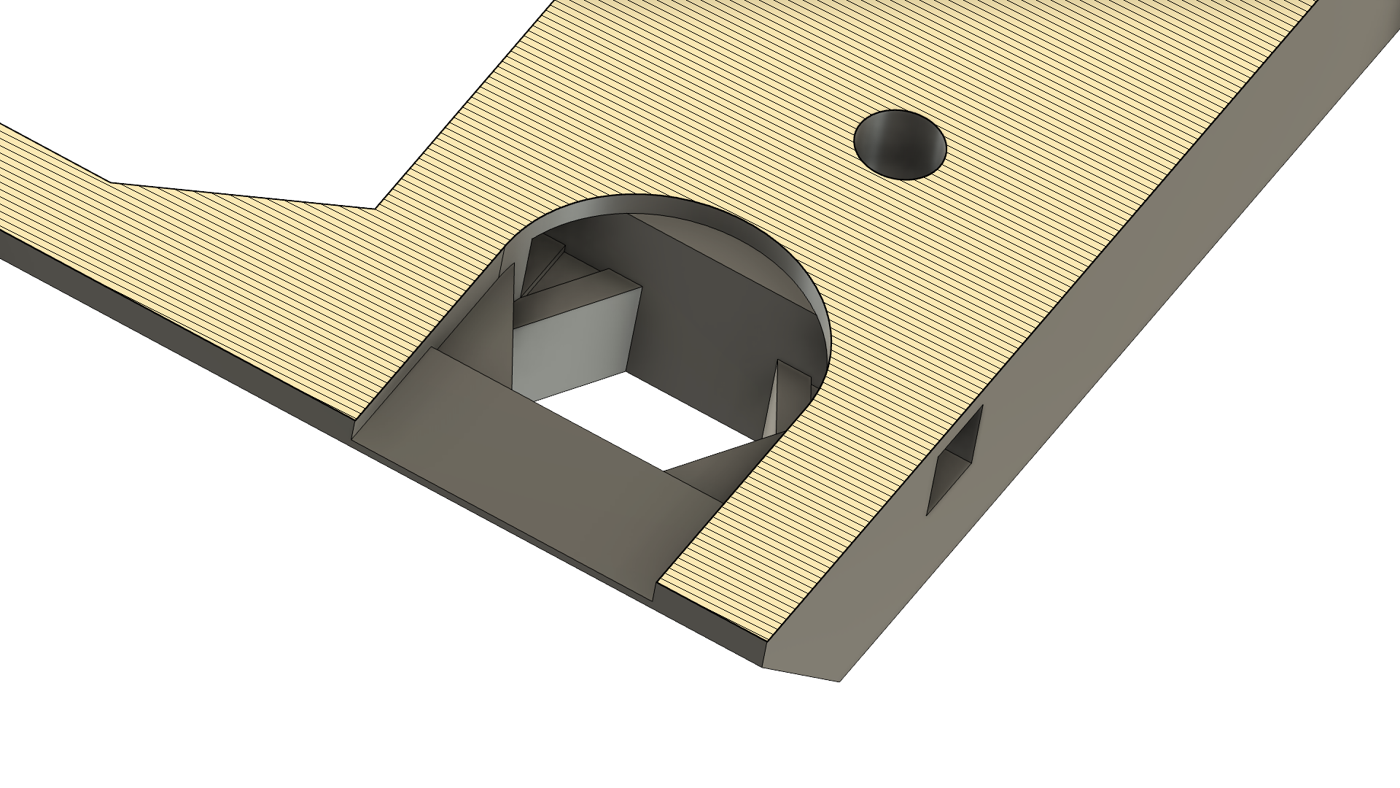
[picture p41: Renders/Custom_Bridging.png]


#### CoM/CoF alignment

This was a huge change, to shift the toolhead to just about the lowest possible, without removing the MiniSB as a possible toolhead option.

By aligning the center of mass of the toolhead to the center of force of the carriage, you reduce toolhead-nod effects that show up on Y-motion resonance tests, as the head rotates about the X axis.

IS graphs are pretty decent in MadMax, and IS effects appear to come from toolhead choice and its weight distribution, more than the use of the MadMax core.

Here's 2 examples from an earlier version, before improvements:

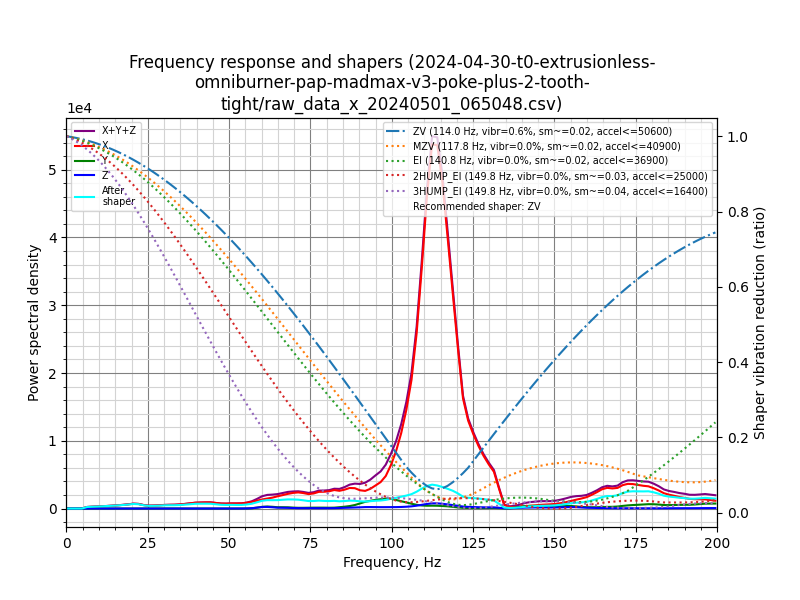
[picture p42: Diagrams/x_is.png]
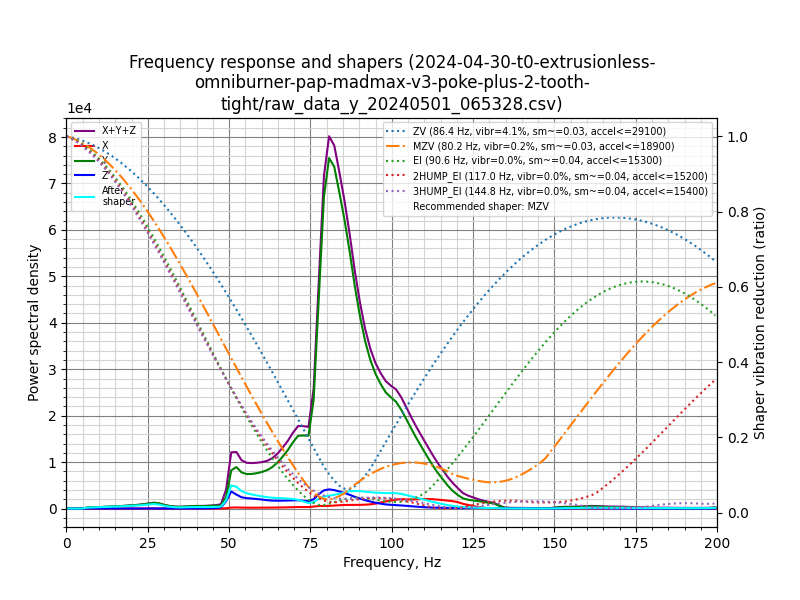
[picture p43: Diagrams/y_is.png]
|  |  |
| --- | --- |

#### Clean airflow
Also part of beta2→beta3 and many other related changes.

Multiple issues arise when hotend airflow is blocked: hotend clogs become possible for cooling-deficient hotends like Dragon HF, but also components nearby heat up more and get softer, causing screws to loosen.  We're trying not to require exotic filaments for a long-term functional design here.

Shifting the head downwards enabled a much more unrestricted path for hotend air.

#### Pins + Screws Maxwell coupling
This is the core of the project and received the most attention and testing.

120 degree vs 90 degree is not an obvious choice.  Prusa XL and Daksh use 90 degree, as it's easier to machine and design.  We kept both and compared them with beta2, but couldn’t see any difference with data.  120 is symmetric and enables easier connection and tighter packaging, so it became the default.

Note that CAD supports a twist about X too, so that you can preload the Maxwell coupling against gravity somewhat, but I wasn’t sure how to make use of that on the plate side.

The coupling uses BHCSes, not acorn nuts; acorn nuts can flake and deform with the thin chrome upper.  However, typically steel BHCSes can wear over many cycles, so we use grease and encourage periodic replacement, until a harder BHCS surface can be found, or slipperier-yet-still-conductive pin material can be found (like bearing bronze, IF it were available in 1/8 or 3mm diameter).

#### “The probe is the coupling, and more”

Having a coupling that enables a probe and does head detection too, is not new; Z-motion designs like TapChanger, Stealthchanger, and ClickChanger do this.  I like that you get so many additional functions from one simple circuit: probing, toolhead detection, crash detection, and potentially even as an endstop too.

#### As large as possible, but no larger, for the coupling
The coupling can’t really go larger, without major changes; the MiniSB third hole and two front holes, combined with wanting the space to screw to bottom of the cowling on both DB8 and MSB, is what drives the dimensions.  

One can absolutely go taller and wider for more stability, if you change those assumptions, but this width seems OK for now.  Yes, it's strictly better to go wider and taller, and you can imagine a more Stealthburner-size-optimized design which isn't encumbered by the choice to support the MiniSB mounting pattern.

#### Off-the-shelf magnets, informed by lots of data
M selection is critical.  
* You want a solid hold, but not so solid that the gantry skips steps when pulling away.
* You also them reasonably sourceable, worldwide.
* You want a size and amount that don't require a larger or heavier setup.

The [Story](STORY.md) page gives more details about the magnet tester and friction tests, and even before automating the testing, a fish scale and simple manual tester provided some great data: [Magnet Testing Gsheet](https://docs.google.com/spreadsheets/d/1X4UAiYmL6JsJxDt9J2394Aaxse2pJNTfiht_ZRcQ6PA/edit?gid=0#gid=0).

Here's a tiny subset of magnet-force testing:

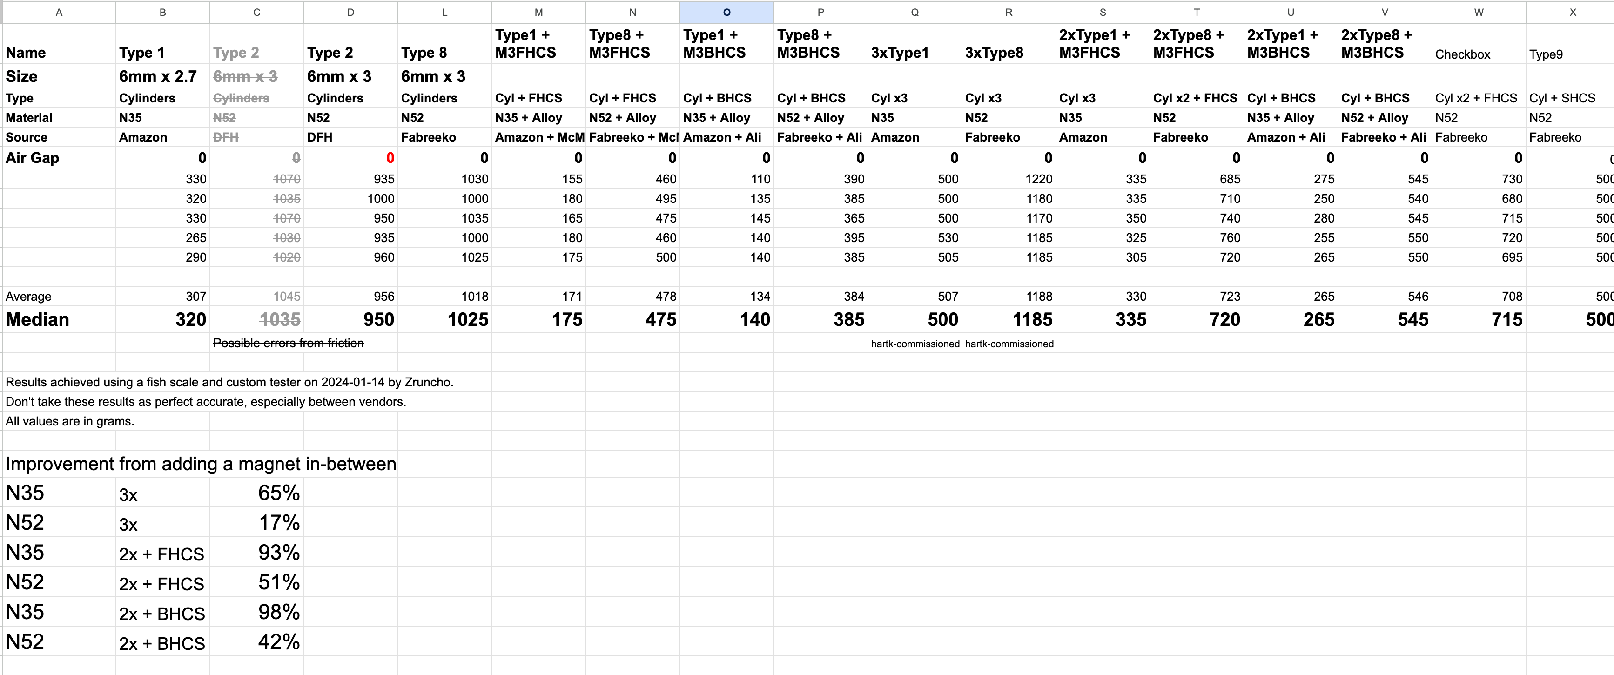
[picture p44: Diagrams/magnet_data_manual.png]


I tried out combos of magnet materials, sizes, orientations, numbers (up to 3 stacked) and even combos of magnets and screws.  

The orientations affect things more than you might expect!

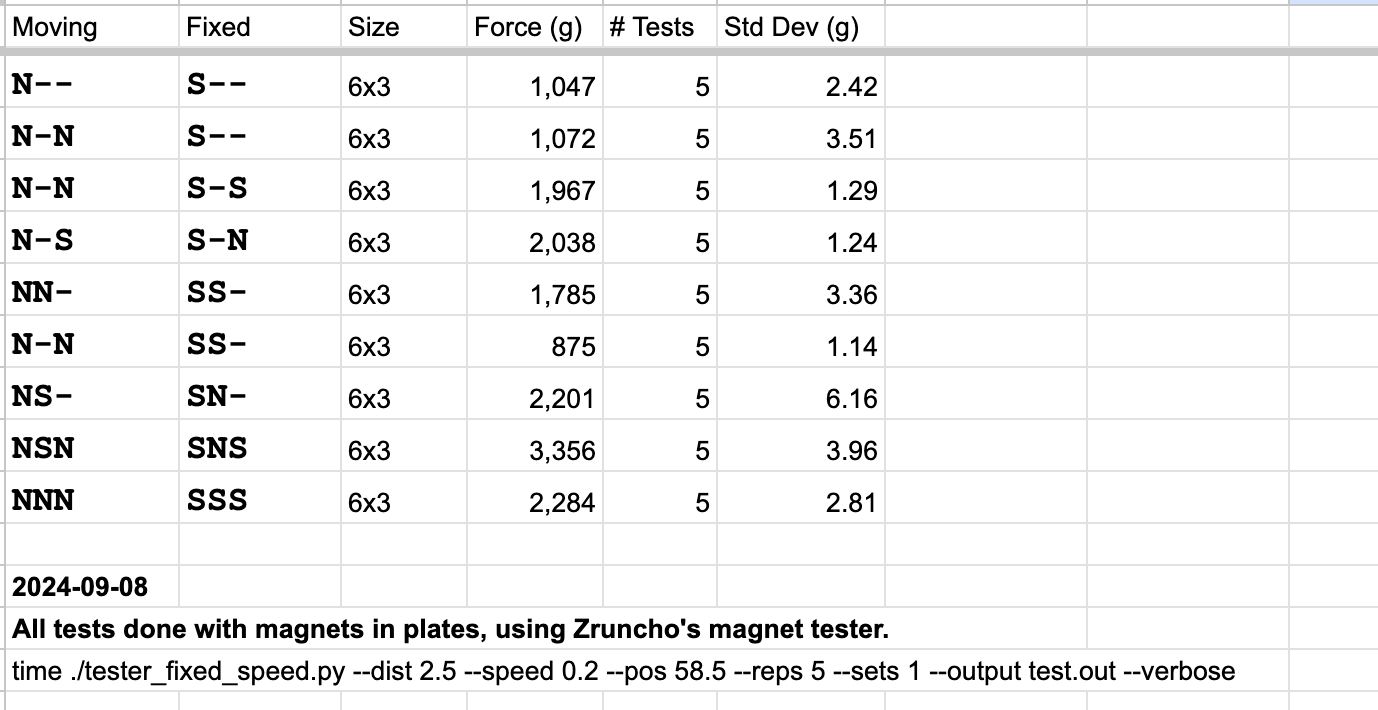
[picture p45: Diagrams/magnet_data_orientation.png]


The end choice was 6mm Neodymium magnets, as they are strong (about 1kg per magnet), are sourceable from multiple locations, small enough, and don't lose too much force at reasonable chamber temps.

A magnet plus a ferrous screw would give more design flexibility, with good hold, but not quite as much.  If you're designing something like this, consider that option.

You do need some air gap that necessarily reduces the magnet force, and some of the force is "lost" to just holding the head up.  Four main magnets is about right and gives some margin to hold up heavier toolheads.

The lower two magnets are not strictly needed, but help provide stability against shaking.

#### Careful hole sizes for improved stability
Voron design guidelines are a great start, in general.  

For example, clearance holes should be 3.3mm, because printers vary and because inner perimeters tend to come out about 0.15-0.2mm smaller than intended.  

However, we want tight fits and minimal motion.  Some screw holes are "twist until it strips" style, which ensures that there's almost no clearance.  An example is the top Maxwell screw.  This is critical for probing, so you really don't want any designed-in slop there.

#### Parametric CAD
Parametric CAD is work, but can totally be worth it, especially when the overall layout of a file has stabilized.  There were about 3 complete redos of the CAD here.  When every little change is painful, because your sketches have dependencies, or so many constraints that Fusion fails to compute them, you may just want to bite the bullet and do a redo.

Here's a tiny subset of the parameters!  Even when a parameter isn't likely to change, it still gives you a way to document some knowledge, so you can refer back to it later.

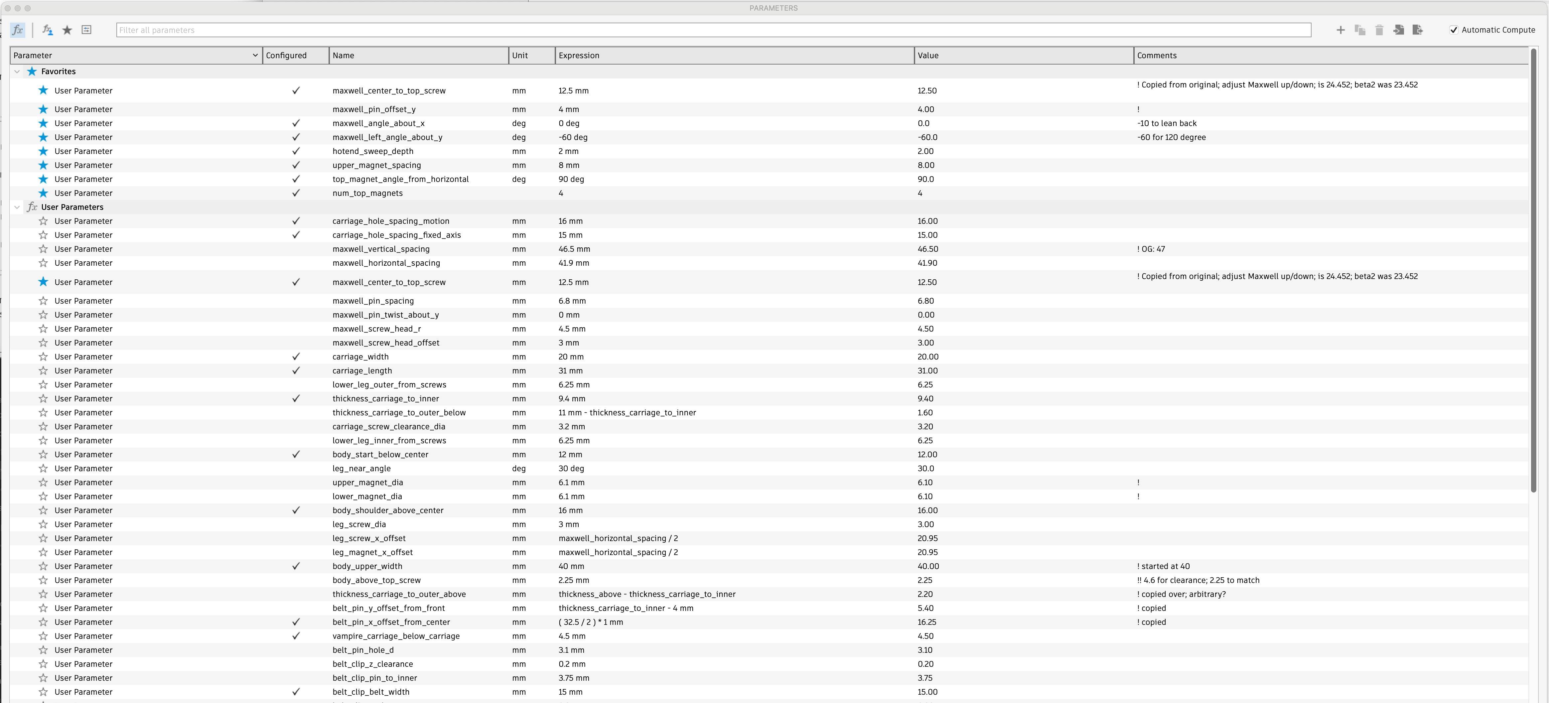
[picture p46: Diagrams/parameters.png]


That's less than 1/3 of the params in use.  It seems excessive, until you compare it to the alternative: not having a way to search for values by name.

HOWEVER, that's the easy part.  The challenge in making a design "properly parametric" is that any shape that varies with a choice - and everything that depends on it - must work when potentially many params change size.  You have to reason about the parameters, and you have to test every change on all the variants.   Speaking of which...

#### Configured Fusion360 CAD
Fusion Configurations helps a ton with a design like the MadMax core that wants to support distinct versions.  Each variant becomes explicit, and much easier to select, so that when you make one change you can confirm quickly, on all designs, that you haven't broken anything else.  You can just force a value for a variant, vs having to make everything an equation - which might not be possible.

You also get to make design features dependent on a config, which is really handy; a design may only need a cutout at a certain size, for example.  When you combine an already-parameteric design with Configurations, you can add new sizes quickly and without too much pain.  An example: the 9mm belt config was pretty reasonable - about an hour, if I recall.

Here's what the Configurations screen looks like:

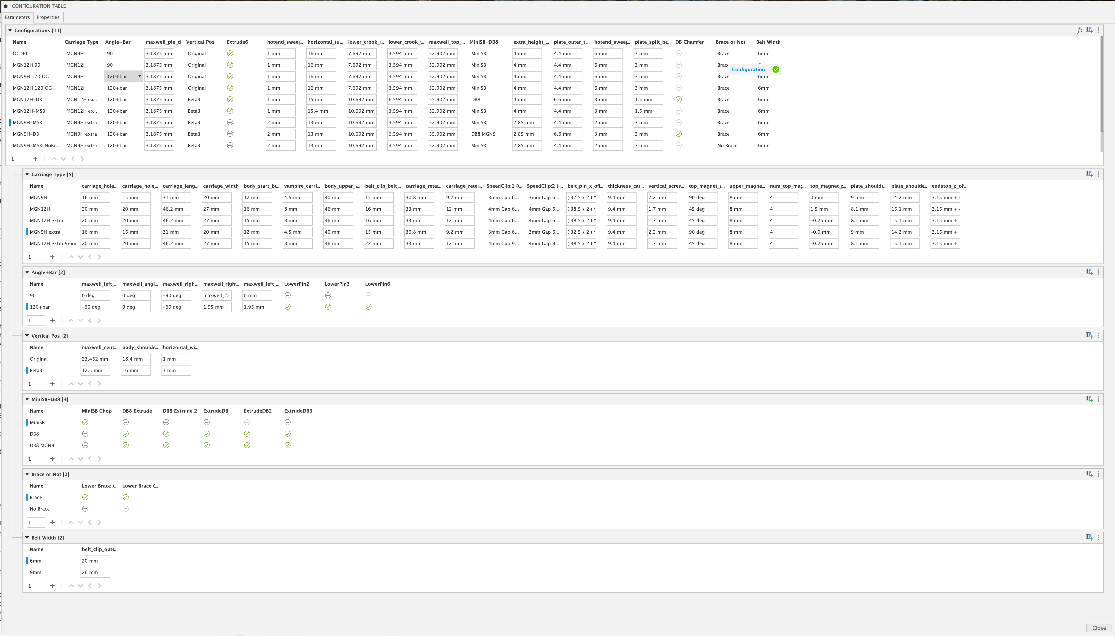
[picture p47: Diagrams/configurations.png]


Yes, it fills up most of a 27" monitor's width.  Many of the top rows are for variants that aren't released, but that's a benefit!  You can track prior versions in one file.  These need to be cleaned up at some point, but you can leave them in until fixed.

#### Reliability Testing
Some of the first tests were aggressive reliability tests for the critical core coupling.  

In fact, a successful 10K-cycle was the trigger for opening up the project to beta testers!

#### Actual print testing is king!

However, the most realistic testing is in the most realistic environment - in printers, especially hot chambers.  We've been doing this testing for over a year, and it's driven all the major changes, mostly around removing the potential for electrical connections loosening over time.

There was one attachment failure from magnet pullout; that required a rethink of magnet positioning.

So far, so good, with two caveats:
* The metal FHCSes on the head will likely cause plastic wear on the docks.  That's expected.  Watch out for it, and if possible, consider higher-wear plastics, periodic replacement, or gentler detach speeds.
* After many cycles of probing, the metal BHCS heads seem to wear in a way that affect probing repeatability.  If you're getting jumps while doing probing of 0.1mm or so, this is a sign.  There's lots more which could be the cause, but in some cases, replacing the screws seems to magically restore the coupling back to triple-zero probing.  Perhaps you have some ideas for surface-treating the BHCSes to improve longevity, using a better grease, or changing to a material like titanium there.  Given that replacing the 2 screws takes a minute and pennies not dollars, I decided to move to release with this caveat.  Plus, if you use Beacon or similar, there's minimal use of the coupling to do probing, so you won't care about it.

#### Spinoffs aplenty
Lots of projects came out of this one, or at least were spurred on by it, as intermediate milestones, or more-broadly-useful projects of their own.  Nudge, Vampire Bat, SpeedClips, a magnet tester, plus a bunch of toolhead mods like DragonBrick, OmniBrick, A4TBrick, and more, including r2pdx's per-print offset-calibration macros.

If you're spinning things off all the time, that's a good thing!

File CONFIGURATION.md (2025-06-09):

## Configuration

In this section, you'll do these steps to get up and running:
* install the `klipper-toolchanger` plugin
* copy over config chunks into toolhead-specific files
* determine and set a few critical calibration values

You should not have to invent anything here!  

You should only have to copy over a few files, then merge them with yours, and resolve the inevitable Klipper errors.

If you experience issues, check the [Troubleshooting](TROUBLESHOOTING.md) page first.

### Install `klipper-toolchanger`

* Always start from a hardware setup which has functional XYZ homing. Everything below assumes that.
 * You already tested homing, right?
* Install Viesturz’ `klipper-toolchanger`
  * SSH to your Klipper system, then install the `klipper-toolchanger` code:
```
wget -O - https://raw.githubusercontent.com/viesturz/klipper-toolchanger/main/install.sh | bash
```
  * Klipper should restart without issue.
  * To enable easy updates: add this chunk to Moonraker.conf and restart Klipper when prompted:
```
[update_manager klipper-toolchanger]
type: git_repo
channel: dev
path: ~/klipper-toolchanger
origin: https://github.com/viesturz/klipper-toolchanger.git
managed_services: klipper
primary_branch: main
install_script: install.sh
```

### Set up toolhead configs

* Look at the `Configs` folder in this repo and select a newer config to start from.
  * As of May 31 2025, r2pdx's configs are a good starting point, with better start macros.  Use that if you can.
* Copy over any missing files as you come across them.
  * Note that `klipper-toolchanger/*` are MadMax-specific sample configs for each toolhead and require a corresponding `klipper-toolchanger` dir.
* Backup your `printer.cfg` file.
* Copy over the bed mesh section below to `printer.cfg`.  If you don’t already have this section, `klipper-toolchanger` will not start. This appears to be a bug in klipper-toolchanger.
```
# klipper-toolchanger expects this section to be present.
[bed_mesh]
speed: 120
horizontal_move_z: 5
mesh_min: 2, 75
mesh_max: 118, 110
probe_count: 3, 3
```
* Modify your `printer.cfg` to reference the provided `klipper-toolchanger/` sample files, like in the sample chunk below; start with one `toolhead_*.cfg` file, and leave the rest commented out for now.
```
[include klipper-toolchanger/macros.cfg]
[include klipper-toolchanger/tool_detection.cfg]
[include klipper-toolchanger/toolchanger.cfg]
[include klipper-toolchanger/toolhead_0.cfg]
#[include klipper-toolchanger/toolhead_1.cfg]
#[include klipper-toolchanger/toolhead_1_as_primary.cfg]
[include klipper-toolchanger/homing.cfg]
```
* If you already have a toolhead-specific config file, make that file the base, and add elements from the config sample.
* Otherwise, modify and review all the added configs, making sure that every printer-specific setting is set correctly for your printer. Edit toolhead-specific files in the copied-over `klipper-toolchanger/toolhead_*.cfg `to match your printer’s pins and values, especially:
  * `canbus_uuid`
  * Extruder pins, rotation_distance, gear_ratio, and currents
  * Z/Probe pin for each toolhead; this will drive toolhead detection, so nothing will happen when you home and try to `UNSELECT_TOOL` later.
  * X endstop pin (same as Z probe), if using an endstop switch there.
  * Note that `[extruder]` in `toolhead_0.cfg` becomes `[extruder1]` in `toolhead_1.cfg`.
* (If using an endstop sensor/switch) Modify `klipper-toolchanger/homing.cfg`’s `[homing_override]` section to comment out the sensorless homing macros:
  * `#_SENSORLESS_HOME_X` → `G28 X`
  * `#_SENSORLESS_HOME_Y` → `G28 Y`
* Comment out any `[homing_override]` section you probably have in `printer.cfg`, as it will override this one, which initializes the toolchanger code.
* Enable forced moves in `printer.cfg` to support the use of `SET_KINEMATIC_POSITION`:
```
[force_move]
enable_force_move: true
```
* Restart Klipper, and resolve any errors that pop up.

### Initial Testing

* In your printer's web interface, ensure:
 * The head probe pin still shows triggered when pressed
 * Endstops still trigger when pressed (especially X endstop)
* Make sure a defined head is physically connected, as the `klipper-toolchanger` configuration assumes this! Otherwise, you get a failure to initialize the toolchanger when doing `G28` the first time after klipper restart, and then you have to restart Klipper.
* Optionally, use the probe as the virtual Z endstop, in which case, ensure a config chunk like this is present:
```
[stepper_z]
...
endstop_pin: probe:z_virtual_endstop
```
... as well as logic in `[homing_override]` (now found in `klipper-toolchanger/homing.cfg`) to move to the center and run `G28 Z`.  Verify this logic is present and make sure the G-codes in that macro are seem reasonable  and match your printer sizes.
* Home (`G28`) should succeed.  That’s a good first step.
* Verify the build hasn't changed, with `PROBE_ACCURACY`.
* Prepare for a `Z_TILT_ADJUST` or `QUAD_GANTRY_LEVEL` run:
  * Change your bed positions for `Z_TILT_ADJUST` or `QUAD_GANTRY_LEVEL` probing, as needed.
  * If you previously used Klicky or another probe with an offset, ditch any macros, as you now have a zero-offset probe.
  * A good tolerance for ZTA or QGL is 0.01 for direct-drive setups, or .0075 for geared or leadscrew-driven setups with higher Z resolution.
* Run `Z_TILT_ADJUST` or `QUAD_GANTRY_LEVEL` twice.

#### Align Docks to Frame and Toolhead
Note that everything here assumes that you’re using identical toolheads with identical builds.  

Note also that the exact alignment may depend on the dock and head choice.  For example, for V0 builds with OmniBurner, the front of the head aligns to the front of the frame, but for other builds, this may not be the case.

* Confirm toolhead-to-dock front-face alignment
  * Power off the printer and bring the head forward, near the docks, or run `M18` to disable steppers.
  * Ensure alignment of the front toolhead face about the X axis (or whatever the dock author suggests); the front face should be vertical,  parallel to the frame.
    * If there is any twist about the X axis (“head nod”), you may not get reliable toolchanging.
      * To adjust this angle, you can add a washer or shim on top or bottom.  However, increasing the magnet gap will reduce the magnetic force, so try to minimize shims, and solve the problem at the root - likely, the carriage.
* Ensure toolhead-to-dock height alignment: with the head near the dock, slide the dock up/down to get the FHCSes centered in the dock holes.  A flashlight or phone light may help.  Crank those screws now, and retighten them after a heat cycle, too.

#### Calibrate Docking Positions
Next, you'll calibrate the positions used in the docking sequence.  These values will go in the `[tool X]`  and `[toolchanger]` sections, which `klipper-toolchanger` uses to drive motion.

You want to get as close as you can to the exact docked X and Y positions.

Fortunately, 0.25mm-0.5mm accuracy is pretty easy to achieve visually.  As long as your homing position is stable (which should be the case for endstop-based homing) and nothing physically blocks the Maxwell coupling, the docking motion should be highly reliable.

The stock MadMax side dock geometry is specifically designed to be forgiving, with support for about 1mm adjustment error in any direction.

| Param Name | Type | Description | Sample Value |
| --- | --- | --- | --- |
| `params_park_x` | Per Head | Position with the toolhead aligned with the dock | 2.8 (for left head) |
| `params_detach_x` | Per Head | Position where toolhead can safely pull back in Y | 8 (for left head) |
| `params_safe_toolhead_y` | Shared | Y position where attached head can move in X and will never hit the other head | 66 |
| `params_safe_shuttle_y` | Shared | Y position with no toolhead attached, where shuttle can move in X and will not hit anything | 15 |
| `params_close_y` | Shared | Y position right before the magnets between carriage and plate start to grab, with docked head | 12 |
| `params_attach_y` | Shared | Y position aligned with center of the dock entrance, at front of docks | 3 |
| `params_fast_speed` | Shared | Speed (mm/min) of free motion; maximize this near machine limits | 20000 |
| `params_path_speed` | Shared | Speed (mm/min) of careful motion near; start low to ensure alignment is correct! | 900 |

The `params_` prefix is a signal to `klipper-toolchanger` to make these values available in toolchange macros.

Explained visually, using A4TBrick with Trident stalagmite docks:

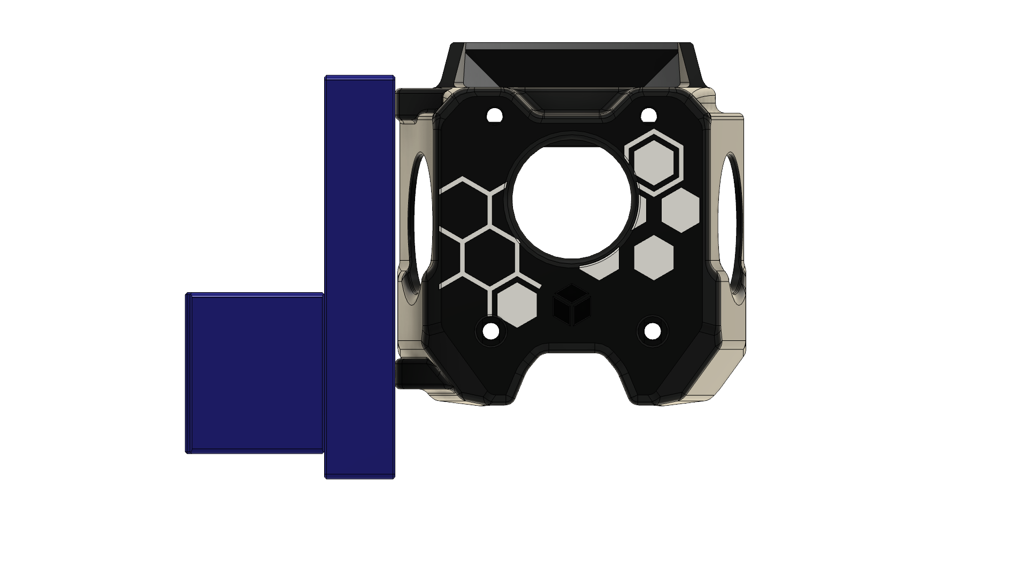
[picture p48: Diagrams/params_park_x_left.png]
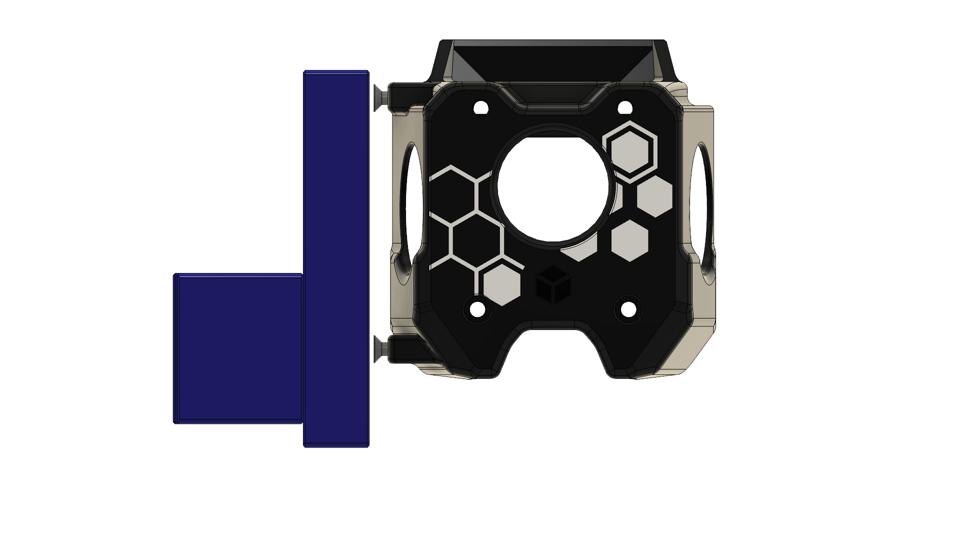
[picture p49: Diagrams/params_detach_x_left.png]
|  |  |
| --- | --- |
| `params_park_x` (left head) | `params_detach_x` (left head) |

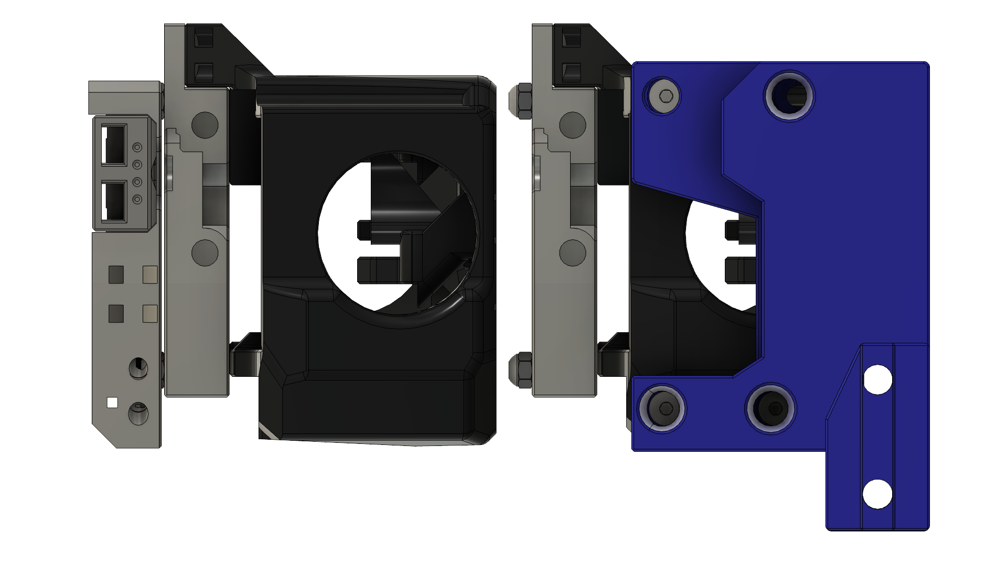
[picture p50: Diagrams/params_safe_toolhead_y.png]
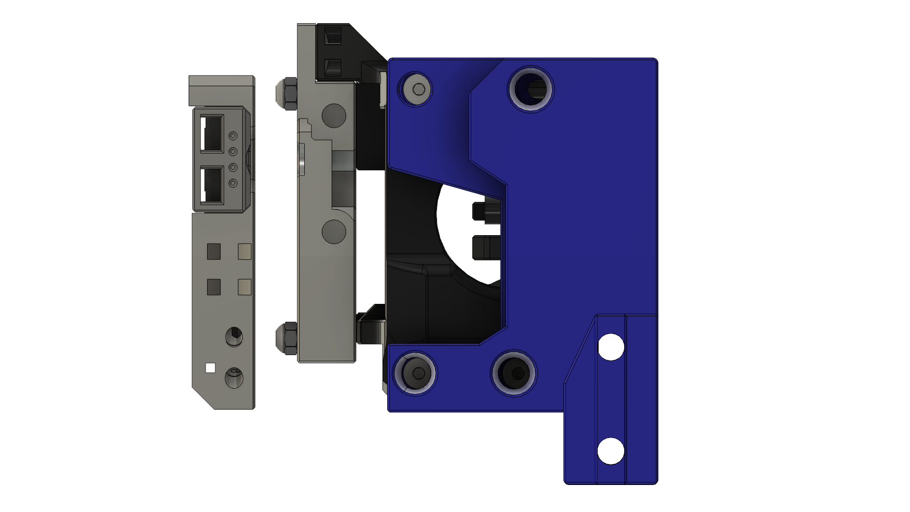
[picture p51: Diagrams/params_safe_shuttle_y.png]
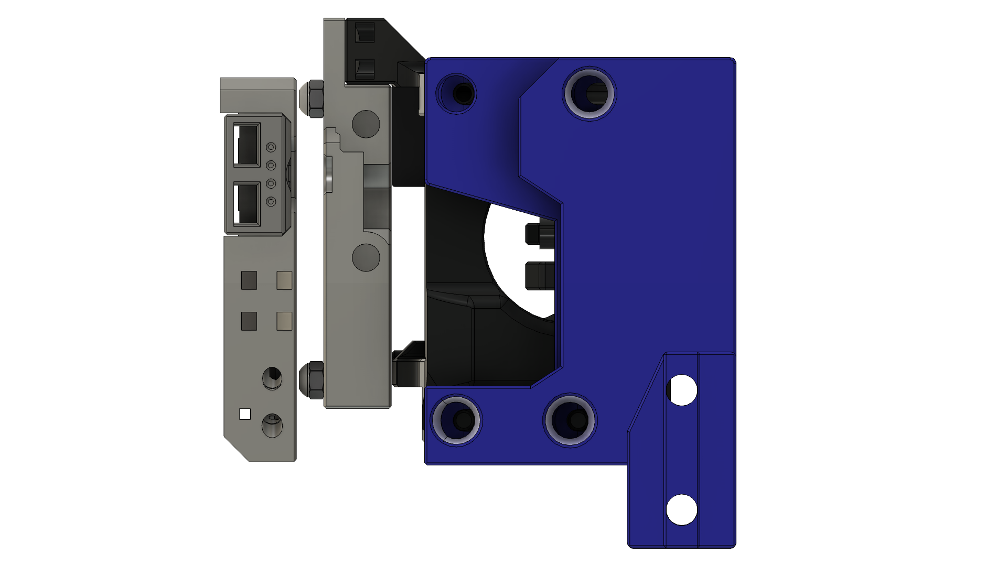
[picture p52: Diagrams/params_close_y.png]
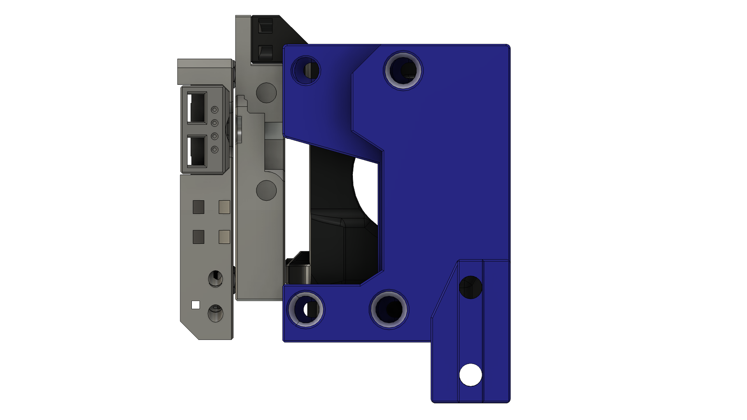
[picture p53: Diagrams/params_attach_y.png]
|  |  |  |  |
| --- | --- | --- | --- |
| `params_safe_toolhead_y` | `params_safe_shuttle_y` | `params_close_y` | `params_attach_y` |

Soon, you will set and modify these values.

The two toolhead-specific values will get added to `klipper-toolchanger/toolhead_*.cfg` files.  For example, in `toolhead_0.cfg`:
```
[tool T0]
params_park_x: 2.8 # Position with the toolhead aligned with the dock
params_detach_x: 8  # Position where toolhead can safely pull back in Y
```

The Y params are shared, and will get added to `toolchanger.cfg`; you'll change the `_y` vals first, to help with setting X values.
```
[toolchanger]
t_command_restore_axis: Z
params_safe_toolhead_y: 66  # safe motion while toolhead is present
params_safe_shuttle_y: 15  # safe motion with no toolhead present
params_close_y: 12  # Y position right before the magnets between carriage and plate start to grab
params_attach_y: 3  # Y position matching the large opening of the slots
params_fast_speed: 20000 # Go as fast as we can # Was 30000
params_path_speed: 900 # Was 1500
```

Take note and refer back here, but don't set the values just yet.  We'll get to them soon.

For the provided configs, T0 is on the left, as you look at the printer, in the minus-X direction; T1 is on the right.  

For all the params below, align visually.

##### Setup T0
* Turn the printer back on.
* Find positions: take notes, then set them in the config after.
  * Find the Y pos for the head as it aligns to the dock.
    * Note that there’s likely to be a Y shift forward after the MadMax conversion, because the core shifts brings the head forward, so your Y=0 zero point may not be physically reachable.
    * Home the head: `G28`
    * Bring the toolhead to the front left: `G0 X10 Y10`
    * …then to the left, until there is about 1mm of clearance from FHCS edge to the dock, then bring it forward until the FHCS aligns with the opening.  Try to get it within 0.5mm or even 0.25mm.  Your eyes should be accurate enough here.  A ruler pressed against the front vertical can help with alignment.
    * This value is `params_attach_y`.
  * Find the X pos for "fully attached to dock":
    * This value is `params_park_x`.
    * The edge of the toolhead shroud should be just touching the dock, or gently pressed against it.  Going 0.25 at a time tends to work well.
  * Find the X pos for "about to park in dock":
    * Find a position closer to the center where the head can safely be pulled back by the carriage, with at least 1mm of clearance between screws and the dock.
    * Since the FHCSes are typically 3mm out from the toolhead shroud, this value is typically 4mm off from params_park_x.  5mm for extra margin is harmless.
    * This value is `params_detach_x`.
  * Bring the head back into the center area of the printer. Never leave it in the front; the next home may swing right and detach the head.  Get in, get out.
    * `G0 X60 Y60`
* Set Values
  * In `toolchanger.cfg`:
    * Set the value for Y in `params_attach_y`.
    * Set the value for `params_close_y` to be much larger, before the magnets grab.
      * 10 mm beyond `params_attach_y` is a good starting point
    * Save, but don’t restart
 * In `toolhead_0.cfg`:
    * Set `params_park_x` to match the value you found.
    * Set `params_detach_x` to match the value you found
    * Save and restart.
 * Make sure T0 is still connected.
 * `G28` to initialize the toolchanger and home.
   * You should see ‘toolchanger initialized’ in the console.
 * **FIRE IN THE HOLE!!!!**
   * Test the values again, or YOLO it, with your finger hovering over the e-stop button.
   * Test detach for T0: `UNSELECT_TOOL`
   * Test reattach: `T0`
   * Test a few more cycles of this and feel proud!  Watch the alignment.  The head should snap back into the dock as the plate separates.
 * At this point, you can just print, as if nothing has changed.  T0 will stay connected if it starts that way.
 * Make sure nothing will hit T0.
   * Adjust offsets to avoid trying to print a purge line that hits stuff.
   * Bed joints and probing locations may need tweaks.

##### Setup T1
 * Repeat same steps for right head, T1
   * Find and set the values.
     * Confirm the Y position with the second head attached.
     * Find the X position for “fully attached to dock”, on the right, and use the same offset for it.
   * … then restart Klipper and try them out.
 * Test T1 switch: T1: `UNSELECT_TOOL`, `T1`

##### Setup T0/T1 Clearance
* Yes, do this for both; if one toolhead is leaning, you don’t want a mid-print collision.
* Bring T1 toward T0
  * Move T1 to the back, then move it to the left, then move it forward, getting it as close as you can to T0, in Y.
  * Take note of the value, and add a bit of margin to it, in case the toolhead is leaning backward from umbilical weight or a missing magnet or screw.
* Move T1 to the right.
  * `UNSELECT_TOOL`
  * `T0`
* Now repeat, for T0 to T1;
  * Move T0 to the back, then to the right, then move it forward, getting it as close as you can to T1, in Y.
* Save value
  * In `toolchanger.cfg`, set `params_safe_toolhead_y` `to the value you found.  Give it some clearance.
  * Save and restart.

##### Test overall reliability and speed
* Run quick attach/detach test: `DOCK_SEQUENCE REPS=10`
  * Measure dock time; Z has sub-1.3s on his MadMax T0 120, and andrewcgr has done sub-4s on a Trident 350 with advanced TMC4671 drivers.
* Consider speeding up the docking sequence before doing any reliability tests.  To speed up those tests, as well as reduce dwell time that can cause drool on prints:
  * Autotune may also be helpful, especially if set to performance, and may help with Autospeed next.
    * [https://github.com/andrewmcgr/klipper_tmc_autotune/tree/main](https://github.com/andrewmcgr/klipper_tmc_autotune/tree/main)
  * Autospeed is perfect for this, and requires only one klipper module, one line of config, and no new parts:
    * [https://github.com/Anonoei/klipper_auto_speed/blob/main/autospeed/main.py](https://github.com/Anonoei/klipper_auto_speed/blob/main/autospeed/main.py)
* Do 100 switches: `DOCK_SEQUENCE REPS=100`
* If this passes, congrats!  You’ve made a reliable toolchanger.
* Almost there!

#### Prepare for Printing
* If you haven’t already… upgrade your PSU, or at least limit maximum power to heaters as a stopgap.  Measure the power at the outlet with an inline power meter (like a Watt’s Up) if you’re not sure.
  * Zruncho says: I always watch power while making big printer changes because it can quickly catch many errors.
  * Watch out for the effects of all that extra power in a small space; at higher chamber temp, especially at V0 scale, may quickly create heat-creep or parts-getting-loose issues that weren't noticed before.
* Re-calibrate your Z offset.
  * When calibrating the z offset, note that these values must now be saved individually to the respective `toolhead_(n)).cfg` files and cannot be saved with `SAVE_CONFIG` (as that function can only write to `printer.cfg`).
  * The typical setup is to calibrate the Z offset of T0 only and use that one always for homing.  You will need to change the homing macros if you want to calibrate using another toolhead.
  * The z offset found in `printer.cfg` will still be applied as well! So either remove that, or if you will only ever home with T0, then set the z offset for each toolhead to 0 and then you can continue to simply use the value found in `printer.cfg`.
* Update ZTA or QGL probing points to a safe default, assuming both heads are present. You don't want one head to hit the other during the print start.
  * No, we don't know of a way (yet) to dynamically change the desired bed-probing points, based on the heads that are present.
* If you want to print with T0, you’re probably done with the config side.
  * Do a quick print with T0. It’s a good test.
* Note - there’s a `toolchanger_1_as_primary.cfg` file, which is similar to `toolchanger_0.cfg`, but it has T1 pretend to be Tool 0.  You can use this config file as a high-availability backup, to not have to change anything, including the slicer, if head 0 has an issue.  
  * Recommended: update the params just like T0, and do a quick print with just T1 acting as T0. Make sure to update the pin used for X homing and Z probing to the other head there.  The only change in the file is the tool number, as `klipper-toolchanger` doesn’t want just tool 1 defined.
* Do your PID tuning, EM, and PA for each new head.
  * Again, after running the calibrations you will have to manually enter the determined values into the respective `toolhead_(n).cfg`.
* Figure out offset calibration
  *  If you want to move on to a first multi-extruder print (or just print with another toolhead than the one you homed Z with), you will need to know offsets between the tools. `klipper-toolchanger` calls these `gcode_offset`s, and they must be set in `toolhead_(n).cfg`.
  * Set one toolhead (typically T0) to zero offset for all three axes.
  * Nudge is the recommended way to measure the offsets of the other toolhead(s), as noted below. However, manual offset adjustment is a second option. It will be less accurate, but can get you printing quickly.
    * Use a feeler gauge to determine the `gcode_z_offset`: adjust `z_offset` until you feel resistance, using 0.005 increments. Swap toolheads and adjust again, comparing values.
    * Alternatively, you can calibrate `z_offset` for either toolhead and then use the difference as the `gcode_z_offset`. * For X and Y there are calibration prints available: [example](https://www.printables.com/model/129617-offset-xy-dual-extruder-idex-calibration).
* Review the provided `PRINT_START`, `PRINT_END`, `PAUSE`, `RESUME`, and other custom macros, to make sure that any position values make sense for your machine.  Sample are provided in `macros.cfg`.

#### Add Nudge
* Follow instructions from the [Nudge repo](https://github.com/zruncho3d/nudge) to build, install, configure, and measure.  Get repeatability values with code from the `printer-experiments` repo if you can (more on this in the Nudge repo).
  * You don’t need to run a Nudge calibration before every print. You only need to use it when changing the tool setup (e.g. replacing a nozzle or toolhead). If you don’t have any overtravel, use one of the magnetic nudge bases to temporarily place the nudge on the printer bed.
  * In a two-toolhead system, `NUDGE_FIND_TOOL_OFFSETS` will produce a single set of values. These are the offsets for T1 relative to T0. Leave these values unconfigured in the T0 configuration, and include the values provided by nudge in the T1 configuration.
* With Nudge, you can do per-print automatic calibration now, thanks to work from beta tester `r2pdx`! See [Klipper automatic offset calibration for tool changers
](https://github.com/joseph-greiner/klipper_tc_automatic_offset_calibration).

#### Print Tests
* Put your badass toolchanger to work. Sample flexes that say, hey, you made a toolchanger:
  * Alternating-layer anything, including a Voron cube - looks trippy and cool
  * [Dual Material - torus with spiraling cross section]( https://www.printables.com/model/190844-dual-material-torus-with-spiraling-cross-section)
  * [Modifier mesh for dual color 3DBenchy](https://www.printables.com/model/908896-modifier-mesh-for-dual-color-3dbenchy)
  * [Dice - Dual Color](https://cults3d.com/en/3d-model/game/dice-dual-color)
  * [Lighthouse](https://cults3d.com/en/3d-model/art/lighthouse-buoy-ship-dual-extruder-test)
  * Tiny Panda - Rob used this one
  * Two-color tagged Voron Cube
  * MadMax poker chip - to be added

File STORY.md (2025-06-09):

# The Story of MadMax

This started off with a discussion with Jon (from the awesome Proper Printing YT channel - check it out!) at OpenSauce 2023 (~June 2023).  Shortly after, I built a little desk toy to play with:

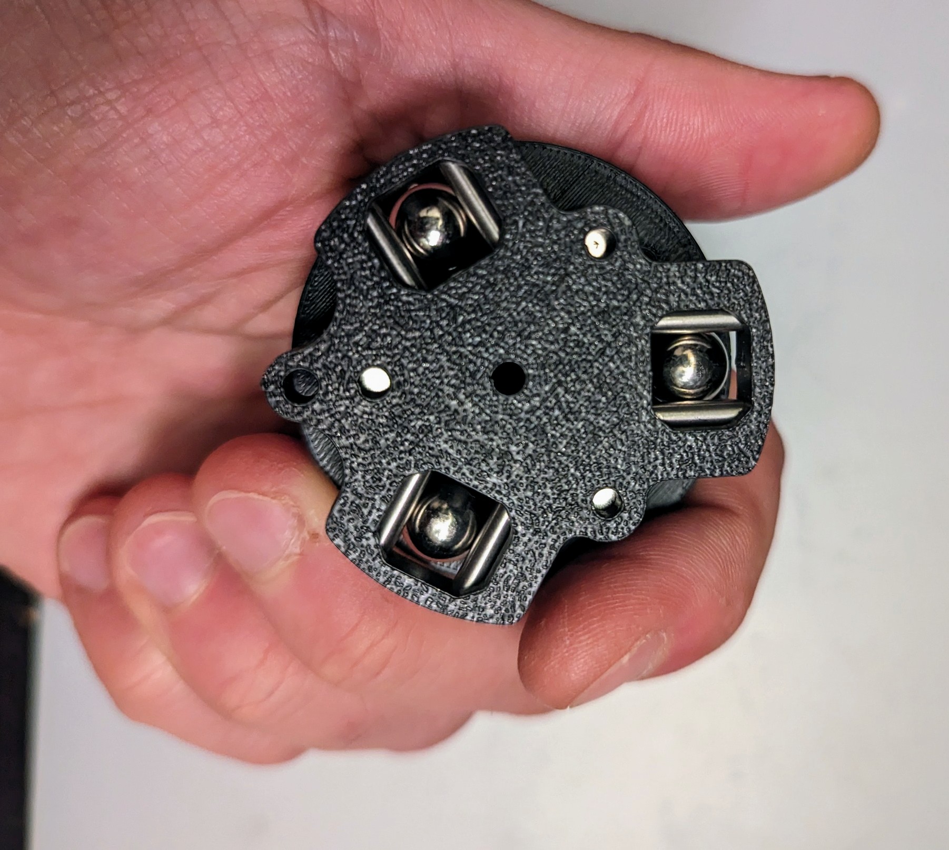
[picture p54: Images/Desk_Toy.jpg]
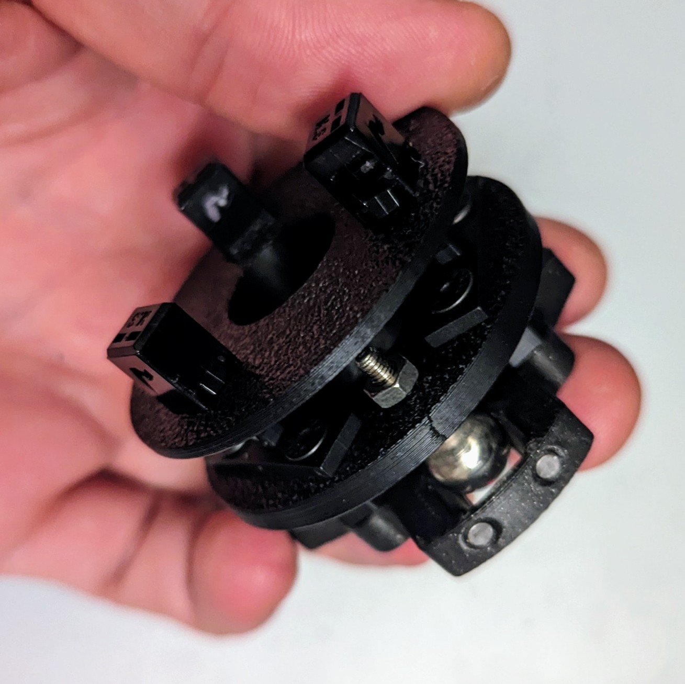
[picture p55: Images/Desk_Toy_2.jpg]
|  |  |
| --- | --- |

A Maxwell coupling is a special kind of coupling - [a kinematic coupling](https://en.wikipedia.org/wiki/Kinematic_coupling) - that effectively guarantees repeatable alignment, which makes it a great choice for systems which need to attach and detach a head frequently.  A Maxwell coupling uses balls and pins; read the [Wikipedia page](https://en.wikipedia.org/wiki/Kinematic_coupling) if you haven't already.

This toy is trying out multiple ideas: a magnetic-only Maxwell coupling (with no positive lock), as well as push-push latches as a dock mechanism.  Simple and fun... but there was a big Q: will the head stay on, or get flung off?

In the initial demonstrator, those M3 ballstuds (borrowed from a Kossel delta printer with magnetic-ball joints from a decade prior) are too big, obviously, and too heavy.  But man is it fun to play with!

I tried out M3s, M4, and M5 button-head screw variants. They all seemed fine, so I went with M3 for the weight savings and packaging ease.  A few N52 magnets with a small gap seemed to have plenty of hold.

Then, I moved to a demo that put the coupling on a modified [Boop](https://github.com/PrintersForAnts/Boop) carriage with pinned belt clips.  I had been testing the carriage for some time already and really liked the ease of use of pins, because when you're iterating on a carriage design, it shortens the iteration cycle.  When you don't know exactly what your design is going to be, this is the most important thing - speed of iteration.

Note - this drops into an existing carriage, replacing the vertical shorty MGN9 "Tap rail" on Boop.  It would never be a final design, but it enables you to get the next critical answer.

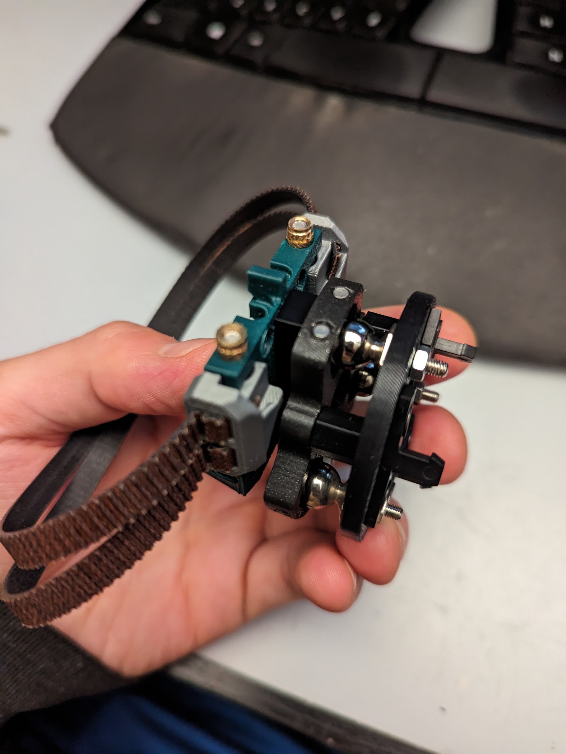
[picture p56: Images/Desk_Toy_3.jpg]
|  |  |
| --- | --- |

I couldn’t see a good way to make this with a top-facing rail, so I tried out a [front-facing gantry mod from richardjm](https://github.com/richardjm/voron-parts/tree/main/voron-0.1/Mgn9h), which had been in use to enable Boop for smaller V0 printers.

So, the next Q this helped answer: will the torque of the gantry suffice to pull it on and off?

I tried it... yes.  And you'd still have plenty of hold for the toolhead.  Running the numbers with my motors, it seemed like maybe 20 lbs of gantry motion force at full motor current, with only a few lbs needed for a solid toolhead hold for a V0-scale toolhead.

That was a sign that a toolchanger could happen, but I didn't like the push-push latches.  Sure, you can pack more heads densely in X, but you really want one big push-push latch, not 3; when 2/3 re-latch, that's bad.  Plus, they need a lot of travel to attach and detach.

Magnets work great, so I wanted to try the simplest dock design I could imagine - one that held magnetically in place, with keyslots:

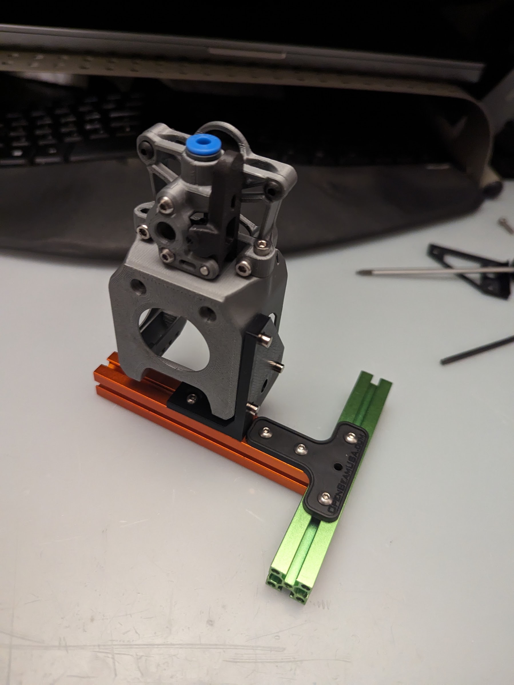
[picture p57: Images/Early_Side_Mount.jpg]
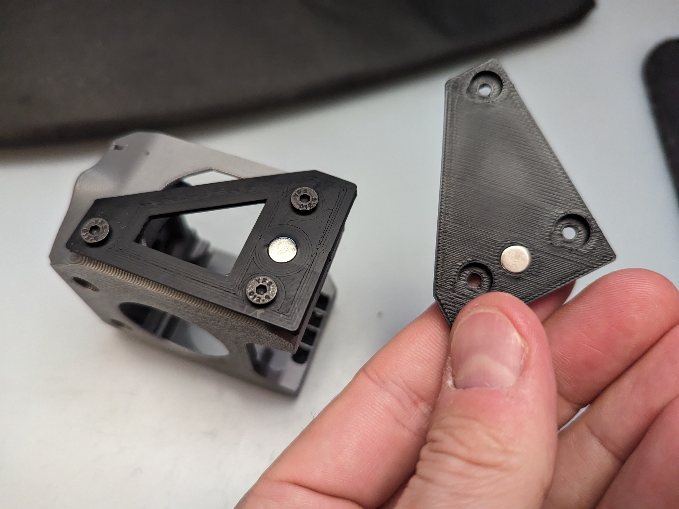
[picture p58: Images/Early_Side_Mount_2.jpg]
|  |  |
| --- | --- |

The simplest design actually seemed to work - ferrous FHCS grabbed by tiny magnets.  Stuff like this is why I keep old unused plastic around!

Then around Nov 2023, it became clear that the toolchanger wasn't the most valuable thing to work on.  

Say you build a toolchanger with this... or really anything with two heads... how will you do nozzle alignment?  I knew that the pain of a TC for nozzle alignment would be shared with IDEX, DG (Dual Gantry), and other two-head printer types, and it was the core reason I had built those but never used them.  In fact, for [Double Dragon](https://github.com/zruncho3d/double-dragon) - a V0 IDEX (!), I used it for a grand total of two months, before it went back to its cave, because I feared the pain of manual vernier calibration prints.  For [Dueling Zero](https://github.com/zruncho3d/DuelingZero) I only used one head in practice.

Calibration is work.  Design is fun.  You can guess which one I, and most people, prefer.

That led to Nudge as a MadMax spinoff... spend 100+ hours to save a 10-minute calibration print :smile:.  Here's what it looks like, in the released form... on an early MadMax that almost nobody knew about.



If you're curious, check out the [Nudge repo](https://github.com/zruncho3d/nudge), which has its own design story, and lots of prototypes - a few of them shown below:

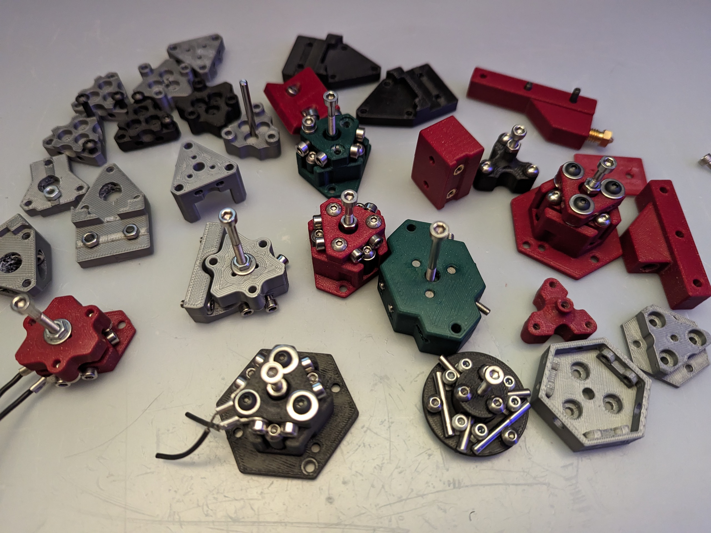
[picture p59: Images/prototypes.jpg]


Anyway, back to MadMax.  I wanted to test the attach/detach motion, which required an actual magnetic Maxwell.  Here we go:

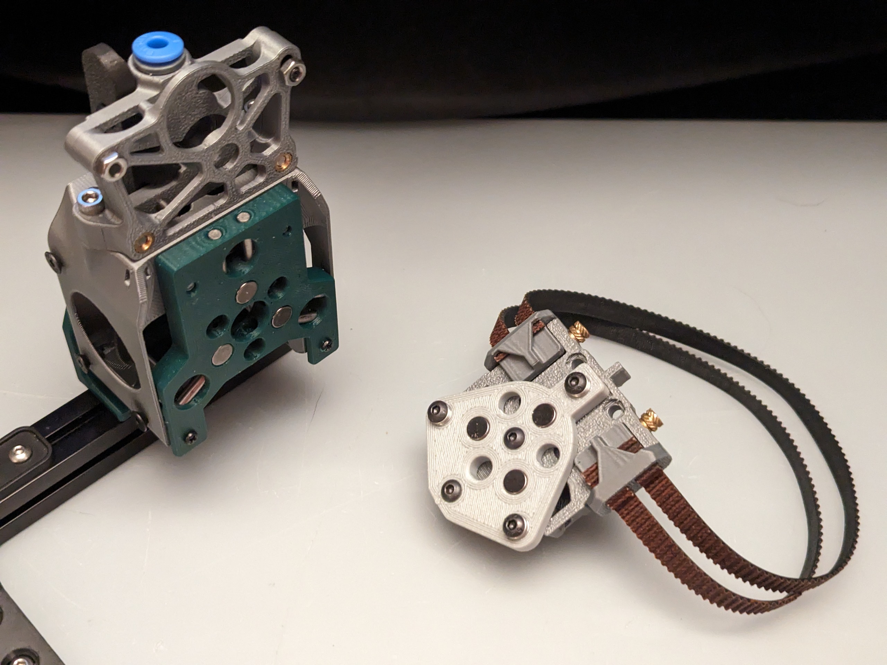
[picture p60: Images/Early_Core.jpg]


Note that the balls are on the carriage and the pins on a plate, which attaches to each head.  The big design flaw this exposed is that you want the magnets higher-up, to better counteract the torque of the head.

I moved to a front dock, thinking it would be more secure; side docking can want to twist the dock itself as the head detaches.  In hindsight, this isn't a fundamental issue, just a reminder to go thicker.  With a front dock you can also mod an existing toolhead, which seemed like a nice benefit for a toolchanger conversion.  Here's how it looked:

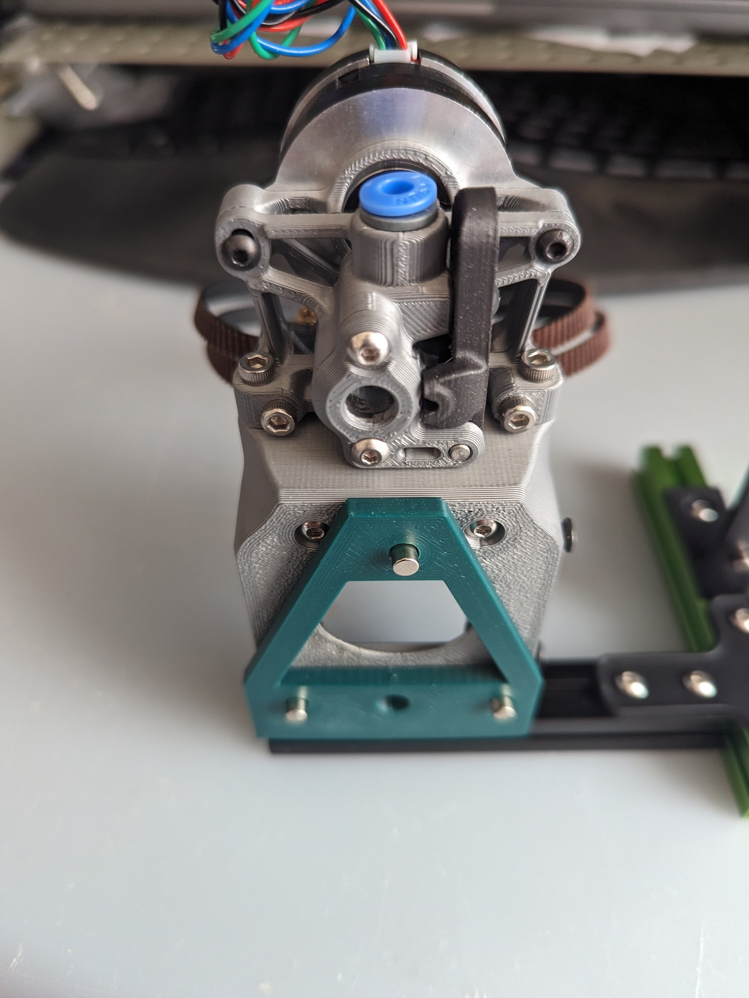
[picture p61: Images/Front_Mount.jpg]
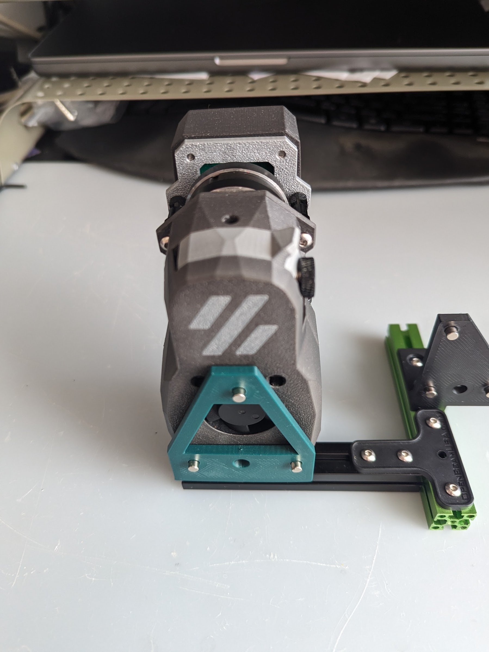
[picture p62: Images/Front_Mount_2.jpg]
|  |  |
| --- | --- |

OK, we can work with this.  A few versions, trying out different magnet placements:

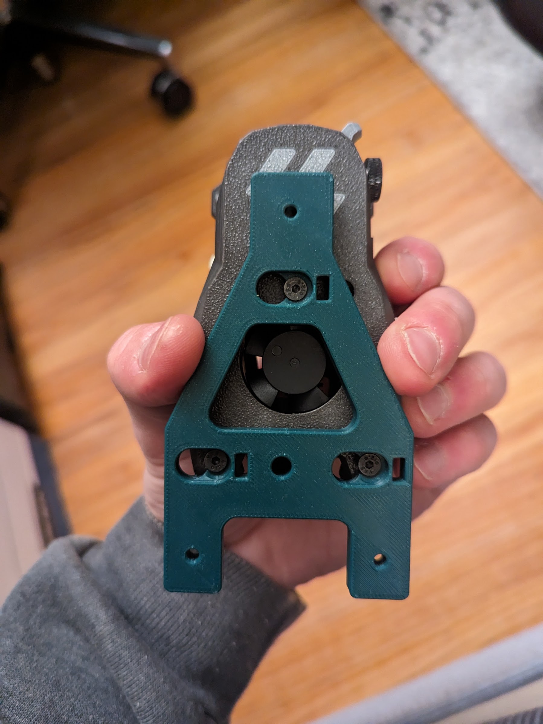
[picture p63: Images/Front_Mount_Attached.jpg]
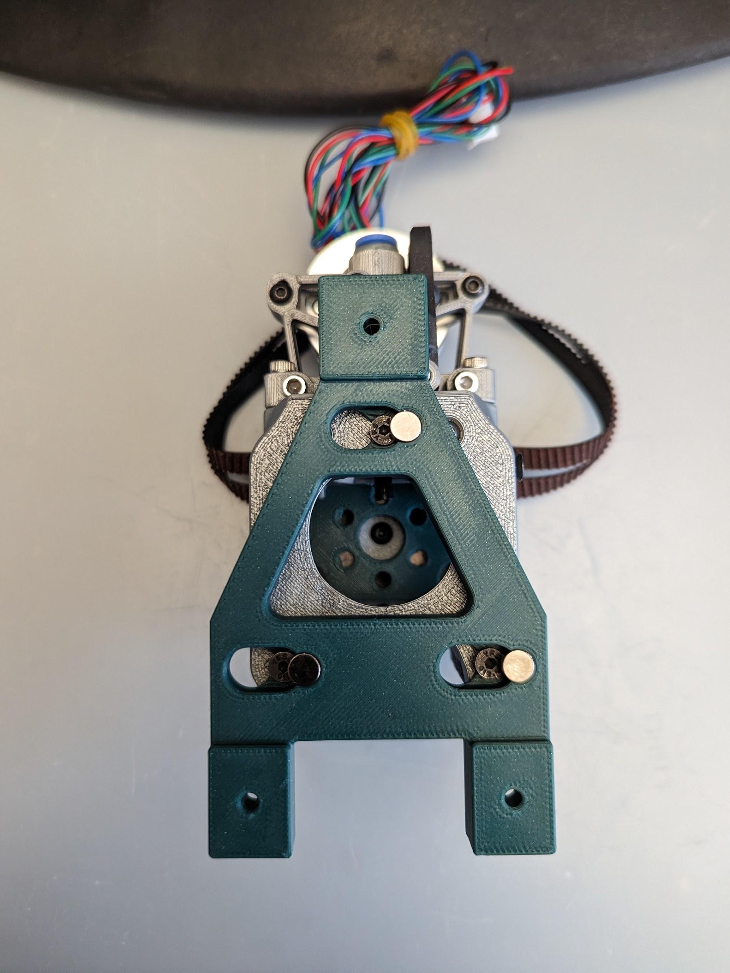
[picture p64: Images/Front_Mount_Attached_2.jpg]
|  |   |  |
| --- | --- | --- |

What I didn't like was that when the head would pull away, it would separate from the plate, but then get pulled back in with a somewhat-loud clunk.  So I tried out a gentler attach and detach, with a magnetic-suspension "pusher plate" that would remove motion after detachment, as well as quiet it down:



Good enough for first attach/detach tests.

|  |  |
| --- | --- |

Note the use of half a Dueling-X 2020 - a single gantry - facing the front, in a 2020 frame made with Rook frame parts, donated by Fabreeko (thanks!).

But I wanted a V0 toolchanger, just because it's kinda stupid and kinda great.  Really compact, and a great developer testbed.



I wasn't fully happy with the front-facing gantry mod and figured I could do the XY joints in a single part and it would be stronger.  

Enter the next spinoff of MadMax: the [Vampire Bat](https://github.com/zruncho3d/vampire_bat) carriage, which paused MadMax, and was released in early 2024.  At that scale, extrusionless is fine!



But the plan all along was to merge the early carriage with its 3 screws, and turn that into a testable toolchanger.

Note here, an early prototype Vampire Bat gantry with single-piece XY joints, but a modified Vampire Bat carriage:



The beauty of a pinned carriage is that you can switch out to new carriages quickly, without resetting belts, retensioning anything, or retesting anything.

I needed a way to do probing, and had been messing around with plastic for that, 'cuz it's fun...



[Poke](https://github.com/zruncho3d/poke) - a single-piece flexure-based drop-in bed probe for V0-compatible heads - was gonna be the way to enable probing with a toolchanger head.  For awhile I used it and it worked on my green Tri-Zero which was becoming the testbed for MadMax:

|  |  |
| --- | --- |

The next change was to flip the orientation.  A few thoughts drove this:
* 3 screws are cheaper for each head than 6 pins and easier to build.
* You want the largest Maxwell coupling area possible, for better stability.  Using the 3rd screw of a MiniSB mount at the top helps.

Here's the comparison.



At this point, I didn't know whether to do a 90 degree orientation, like the PrusaXL and Daksh use, or a more traditional 120-degree orientation.

We need a real dock, though, for a V0.  I went with a simple, strong, blocky design.

|  |  |  |
| --- | --- | --- |

I always thought the "Wideboy" MiniSB mod - with plates added to it - looked cool.  That gave the flat surface and known-good geometry for the FHCSes that go to the dock.



But... it didn't all fit AND have space for the travel Nudge needed in the center.

So I moved to a toolhead from Kevinakasam called OmniBurner, and chopped the sides to enable the FHCS mount; at 54mm, vs ~58mm, I had the space needed to put a Nudge in front.

You can see the work-in-progress below, also with a first attempt at a Bricked toolhead style, where the toolhead board is in front of the extruder.  This pairs well with extruders that don't need much front space, like the PapLite extruder shown here in the center.



Add some front shrouds...



Now we have a complete toolchanger, with potentially automatic calibration, and can move to test prints!



It's not impressive, but it's from the world's smallest, least-practical toolchanger, so I'll take it.



It looks cool at night, accidentally; the two Huvud toolhead-board versions each had different lights, and the shrouds make the light more interesting!

|  |  |
| --- | --- |

Surprisingly, the prints had near-perfect calibration, out of the box, with only Nudge.

|  |  |
| --- | --- |

This is extremely good layer stacking.  The coupling is certainly not hurting print quality: the most important part, and largest unknown, seemed fine.  The seams are clean too.  But, all this was with a prime tower to catch drool, and you really want blockers and brushes to minimize drool while the heads move to the prime tower.



This was the first attempt using silicone baking brushes, chopped down.  I didn't like that they blocked the view when you wanted a one-extruder print.

At this point (June 8), we have something worth printing, and the Closed Beta began for real, with the goal of getting more builds, evolving the parts, and figuring out whether this was even worth releasing.



OpenSauce 2024 was a big motivator to get a real test print to share with Voron and YouTube folk.



Seeing the Voron Phoenix IDEX in person, seeing a Prusa XL, seeing Jon's crazy dual gantry printer, talking to Voron Crew... it's all motivating stuff.

Excited, I went home and spent the night getting something more than a basic cylinder test.  Went to sleep late, after a failure partway through an alternating-layers Voron Cube print:

|  |  |
| --- | --- |

I looked at the detached head:



You see the issue?  Yeah, in a hot chamber (from my first long two-extruder print), all that heat in that tiny space meant that the plastic around the magnet relaxed, and it popped out.

So the next day at OpenSauce, I showed the coupling and asked everyone I saw - "how would you solve this?" - and got something like 20 unique answers, some hilariously impractical, and some straightforward and good. Answers ranged from Tom Sanladerer's suggestion of special metal-plastic glues, to using magnet wire, to putting a bigger magnet on one side.



BTW, Phoenix is HUGE.  This was before the rush of people.

That night, a quick fix with a drill, and we had a solution.  The print succeeded, and it was glorious.  Gemma-cat agrees.

|  |  |
| --- | --- |

What was the change?



The critical improvement was FHCSes to hold the magnets by their edge chamfer.  This is a simple way to avoid glue and hold them in at higher temps, plus avoid any dependence on a specific printer, which affects the level of plastic grip.  It's just bad to rely on plastic grip alone, anyway.  It will inevitably fail in a hot chamber.

Lots of testing later from the beta team, and the focus had moved to long-term reliability and reducing probe force.  

The set screws holding in the wires - used for head detection through the plate, for the toolchanger firmware - would come loose with time.  Same issue as Poke... metal into plastic is bad in a hot chamber.

At this point, many of us in the beta were doing Maxwell probing, where the coupling itself is the probe sensor, as it slides up, and the pins and screw heads break their connections.  Surprisingly, you can get triple-zero probing here - 0.000x mm Std Dev - which is vastly better than needed.

But, that probing wasn't perfectly reliable over time.  There's a tradeoff which affects probing reliability.  If you increase the magnet force, potentially you get a better coupling, but potentially at the expense of higher probe forces, which may hurt repeatability.  Without numbers, it's all guesswork. That little gap also affects force, heavily.  What should it be?

The next MadMax spinoff was a load-cell-based magnet tester, which could be put into a printer to measure the drop-off in magnet forces, as the temp rises:



In the tester, a motor turns a lead screw, which pulls on a magnet, and you watch the force drop off as the magnets pull away.  Look at the peak, and that's the magnet force.  You can measure magnet force with single-gram precision, up to multiple Kg, with only $12 of Amazon load cell parts (HX711 board), plus a Raspberry Pi and a few hundred lines of Python.

The tester justified the time investment.  It quantified the drop in force at chamber temps, and showed that no, we don't need higher-$$$, more-exotic Samarium Cobalt magnets here.  At our chamber temps (sub-70C), N52s are still stronger.



Don't over-index on the little dip; plastic bits in the tester probably started creeping loose around 64C, and the USB hub died.  Keep your consumer electronics out of the oven...

The tester was soon generalized to other purposes, like measuring the friction on various pin materials, with a little sled thing, weighted by a stepper:



I tested everything McMaster had in 1/8" rod: Steel, PTFE, ABS, PP, POM, Nylon, Graphite, and Greased Metal.



Here's an example graph:



... and that's why we spec Acetal (POM).  Low friction, high durability.  Less probe force than metal pins; not as soft as Teflon (PTFE), which deforms quickly from magnet forces.

I could even measure magnet forces from probing, to quantify the effect of gap changes and other things.  That required some upgrades to the tester, to move from flexy V-wheels on V-Slot extrusions, to parallel MGN9 rails:

|  |  |
| --- | --- |

I was so happy when I could "call a shot" - take measured magnet force data, combine it with measured friction coefficients, and predict a probing force change.  This helps you consider design tradeoffs, like "head grip" vs probing force.  It's amazing when the model matches the measured reality.  Then, you truly understand what you have, and how to tune it.

By this release, SpeedClips where a thing too - yet another spinoff:



SpeedClips open up the clip aperture, so you can adjust the belt position quickly.  They're awesome.

All this knowledge folded into a Beta2 release, with a completely new CAD, which uses Fusion configurations to enable 90 and 120 degree versions, as well as MGN9 and MGN12 variants, in one file.



Relative to beta1, the main changes were:
* MGN12 support
* 120 degree "official" support
* vastly better wire routing in the plate (though the plate!)
* locking thumbscrew support for IS testing
* optional carriage magnet locking screws to prevent heat-cycle-induced pullout
* nuts/screws instead of set screws on plate
* bar option instead of wires and set screws on carriage
...and a bajillion small dimension changes.

Video here: https://youtu.be/EqUv1yK-KEs

It was all shown for the first time, in person, at Reno VICE in October 2024, as part of the Pacific Ant Fleet's visit (my cadre of small printers). Note that Dueling Zero, on the right, is using the MadMax core here.  For over a year, I've been dogfooding this thing.



More beta members, more lessons: connection reliability, build speed, and print quality are the big focus areas, still, which led to Beta3 in October 2024.

This one had a complete CAD redo for maintainability, plus extra sizes added (MGN12 w/ 9mm belts), and eliminated formed threads.

At this point, it becomes clearly that this is not that crazy.  Lots of people are succeeding with builds and impressive prints.
Some surprising benefits from living with it for a year:

* Maintenance ease - grab a head, inspect it, and put it back, no tools needed.
* No tuning vs MMUs - no tip tuning, no distance/speed tuning.  Just offset calcs, but those are automatic with Nudge.
* Actually pretty cheap with cheap hotends (TZ-V6 is $20, EBB is sub-$20) - can cost less than an MMU setup.
* Mainline Klipper has benefits.

Still, there's an issue... creep on connections, especially on the plate, especially in a hot chamber.  If you tighten a screw hard, the plastic will relax at high temps, causing a loosened connection.  Then to "fix" it, you tighten it harder, creating a frustrating downward spiral.  To avoid this, in early 2025, Beta4 moved to heatsets on the plate, with ring terminals and crimps, and clearance for those.  A small change, but it eliminates creep worries on the plate.  

At this point, if you're still reading, learn more about the final design from the [DESIGN.md](DESIGN.md) section!

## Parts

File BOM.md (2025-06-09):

## BOM.md
Prelim BOM - boring, by design!  Reasonable, with the exception of the Acetal pins.

### Carriage Parts
 * Maxwell Pins
   * **2x metal pins**
     * Preferred: ⅛” dia x ½” length
       * Amazon: [uxcell 1/8-Inch x 1/2-Inch Dowel Pins](https://www.amazon.com/dp/B09M84DNT6)
       * McMaster: [Dowel Pins](https://www.mcmaster.com/products/dowel-pins/dowel-pins-2~/dowel-pins-1~~/length~1-2-2/length~3-8-1/length~7-16/diameter~1-8/diameter~0-125/material~steel-2/material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): [416 Stainless](https://www.mcmaster.com/98380A471/) OR [316 Stainless](https://www.mcmaster.com/97395A441)
     * ⅜" length is acceptable too
     * Yes, you can rough-cut bar stock, or even have them stick out a bit in both directions. It’s only the center part touching the BHCS that matters; ends can be a mess and nobody will see it.
     * If you find 3mm locally, that’s fine too.  You’ll have to export your own STLs in that case.  In that case, 12mm is preferred, but 10mm or 14mm will also work.
   * **4x plastic pins**
     * Best: POM (Polyoxymethylene) ⅛”: sold as Acetal, Delrin or Kocetal. POM-H and POM-C should work equally well in this application.
       * McMaster: [Pre-cut 1/8" x 1/2" pins](https://www.mcmaster.com/97155A426/) OR [1/8" stock](https://www.mcmaster.com/catalog/130/4126/8497K11) which cuts with large wire cutters.
     * Probably fine: steel pins, same as above, but will yield higher force.
     * Not OK: Teflon (PTFE) - deforms too quickly.
     * If you find 3mm locally, that’s fine too.  You’ll have to export your own STLs in that case.
     * These are English sizes because we couldn't source 3mm Acetal rods.
     * We have data (measured friction coefficients, probe forces with various materials), and some is at the bottom of [STORY.md](STORY.md).
 * Belt Pins
   * **2x 3mmx35mm steel pins**
     * Rounded ends are best (look for "locating dowel round head" or similar), but the usual chamfered pins work fine too
     * AliExpress: [3mm x 35 pins](https://www.aliexpress.us/item/3256803440853860.html)
     * Amazon: [uxcell 3mm x 35mm Dowel Pin](https://www.amazon.com/gp/product/B07M9TS54L)
     * McMaster: [3x34mm, sold individually](https://www.mcmaster.com/91595A117/) OR [3x36mm, pack of 25](https://www.mcmaster.com/91595A140/)
     * Alternately, use M3x30 SHCS/BCHS you have lying around.
     * Alternately, use M3x35 SHCS/BHCS with a nut or two on top.
     * Alternately, use ⅛“ pins; requires drill-out of plastic and will affect your choice of tubes. Example: McMaster [hardened steel pins, ⅛” x 1⅜“](https://www.mcmaster.com/98380A478/)
   * **2x M3 “Voron standard” heatsets**
     * Will fit onto pins after being drilled out.
     * Different spec M3 heatsets are fine
 * Belt Clips (a.k.a. SpeedClips)
   * **2x M3x10 BHCS**
   * **2x MakerBeam XL T-nuts** (from V0 parts list)
      * Amazon: [MBXL T-nuts](https://www.amazon.com/MakerBeam-XL-MakerBeamXL-15x15mm-Diameter/dp/B06XHQHD4H)
      * Can make your own, too, in a pinch.
   * **2x Metal Tubes**
     * These are metal tubes, into which the belt pins go.
     * Width: Two sizes are recommended:
       * Metric: 4mm OD, 3.2mm ID
       * English: 5/32" OD (3.97mm) x 0.014"
     * Length: varies by the width of your belts and the gap between the belt paths.
       * File to length.  A printed cuboid with matching sized hole for your tubing’s OD works great here to get a flat file and do that quickly, vs holding it with your fingers.  Reaming/using a drill bit on the cut tube will make it smooth
       * MGN9H: 14.5mm (slightly below 15mm is fine)
       * MGN12H with 6mm belts: 15.5mm for larger 4mm belt gap.
       * MGN12H with 9mm belts: 21.5mm
     * Material:
       * Stainless steel is best
         * Stainless will be stronger, but slightly harder to cut (esp. with a hacksaw) and file. Fortunately, the walls of this tubing are fairly thin, so it’s not so hard to work, even using hard stainless steel.
       * Aluminum is fine
       * Brass is OK
       * PTFE: only in a pinch, until the real parts arrive.
         * Yes, you can use drilled-out 4mm / 3mm PTFE tube, but it will deform under the forces and experience higher friction.
     * Sources:
       * Local hardware stores
         * Ace Hardware: K & S Precision Metal #8103 Round Aluminum Tube from Ace Hardware
       * McMaster:
         * [Welded Tube](https://www.mcmaster.com/50415K59/) (welded, not smooth bore, but confirmed to be OK)
         * [Welded Tube, 4mm OD, 3.5mm ID](https://www.mcmaster.com/50415K61) (acceptable also welded).
         * [316 Stainless](https://www.mcmaster.com/89785K816-89785K217/)
         * [304 Stainless](https://www.mcmaster.com/89895K716-89895K217/)
 * Main electrical connections
   * **2x M3x8 stainless FHCS**: can be 10mm too, but MUST BE CONDUCTIVE.  No black alloy here.
   * **2x M3 shims**: 0.5 thick, 7mm OD
   * **2x M3 nut**
 * Other
   * **4x M3x8 SHCS**: for carriage attachment (BHCS OK as workaround)
 * Homing (**read carefully - depends on type**)
   * Sensored (endstop-based) homing (recommended)
     * **~120mm wire 22-26 gauge**; must be less than 1.8mm OD
       * [AliExpress wire](https://www.aliexpress.us/item/2251832766791205.html)
     * **1x Omron D2F**: or similar.  Usual “Voron standard” switch for X-endstop (plus endstop of choice for Y)
     * **2x M2 self-tapping screws**
   * Sensorless homing (not recommended)
     * **60mm wire 22-26 gauge**; must be less than 1.8mm OD
       * [AliExpress wire](https://www.aliexpress.us/item/2251832766791205.html)
 * Magnets
   * **6x 6x3mm N52 (Neodymium) magnets**: actual amount to use will depend on toolhead weight and bed stability (4-6x)
     * **THESE MUST BE REAL N52. Do not try Amazon or AliExpress.  Use known-good vendors.**
     * Example: [Fabreeko N52](https://www.fabreeko.com/products/n52-neodym-magnet-6x3mm-schwarz)
 * Optional Magnet-Retaining Screws (required if used in chamber; probably optional if in free air)
   * **3x M3x8 FHCS**; can be 10mm depth.
     * MUST BE 5.8-5.9mm head dia, not 5.5mm head dia.
     * Black alloy steel or shiny stainless are both OK here; they’re not forming an electrical connection.
   * **3x M3 nuts**

### Plate Parts (xN): per head
NOTE: **per head totals**, below:

 * Maxwell Coupling
   * **2x M3x8 BHCS** - must be conductive (stainless), not coated alloy
   * **1x M3xX** for top screw (depends on head choice)
     * Does not need to be conductive.  MUST have no writing!  MUST not have a rough surface!  Needs to be shiny and smooth.
   * **5x M3 nut** (3 should be in 2.2-2.4mm thickness; find 3 that match)
 * **2x M3x8 BHCS** (lower toolhead attachment)
 * **6x 6x3mm N52 magnets** (see note for carriage)
 * **4x M3 “Voron standard” heatsets**
 * **2x M3 Jam Nuts** (1.8mm thick) OR 8x M3 6mm-OD shims (0.5mm thick)
 * **2x ring crimp terminals with 3mm hole**
 * **250mm 2-position zip wire** for connection to toolhead board; see note on sizing, in carriage section
 * Optional Magnet-Retaining Screws
   * **3x M3x6 FHCS**; alloy or steel OK
   * **3x M3 nut**

### Dock- and toolhead-dependent parts
Below are starter requirements.  Make sure to check with your dock/toolhead vendor first.

* Docks (x2): **per dock** below; depends on specific dock and printer, but commonly:
  * **3-4x 6x3mm N52 magnets**
  * **M3 or M5 mounting screws**
  * For Xol/A4T dock by `andrewmcgr`:
    * Each dock:
       * 8x M3x8 SHCS or BHCS
       * 8x Voron M3 headsets
       * 2x M5x10
       * 2x M5x20
       * 4x M5 extrusion nuts, 3x 6x3mm magnets
* Second Toolhead - check with toolhead vendor first:
  * All the same stuff a typical hotend will have (fans, hotend, toolhead board, bowden, screws, ECAS, …)
  * DragonBrick/RapidBrick - per head
    * 3x M3x8 FHCS - must be alloy!
  * XOL/A4T by `andrewmcgr`:
    * Each toolhead: 3x M3x8 or M3x6 FHCS (must be strongly magnetic, i.e. steel and not stainless), 1x M3x16, 1x M3x12 SH or BH, 2x extra heatsets
  * AntHead
    * See AntHead repo
    * OmniBrick - per head
      * 4x M3x8 FHCS - must be alloy!
      * 2x heatsets (add in post; a bottom rear of cowl)
      * 1x M3x6 FHCS (for Huvud shroud)
* Nudge (optional)
  * Not technically required, but highly recommended.  See its GitHub page: [https://github.com/zruncho3d/nudge](https://github.com/zruncho3d/nudge)
* Additional Spool Holder
* Additional Bowden/ECAS
* Upgraded PSU
  * An upgraded PSU might be necessary. Either go for a comfortable margin or buy an inline power meter (like a Watt’s Up) and measure consumption if you’re not sure.

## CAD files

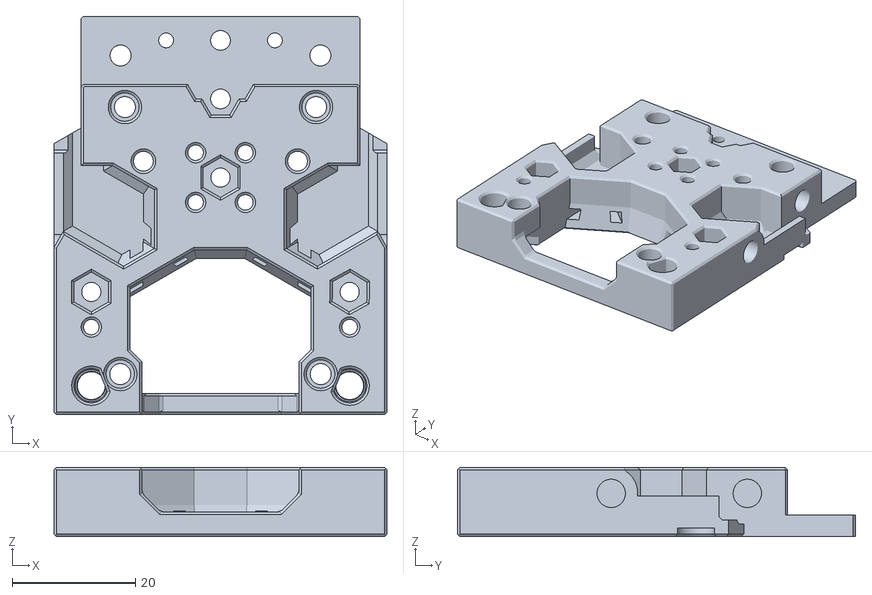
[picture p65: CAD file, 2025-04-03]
User Mods/andrewmcgr/XOL-A4T-Cartographer/STL/Plate Assembly.stl
54.0 x 64.6 x 11.2

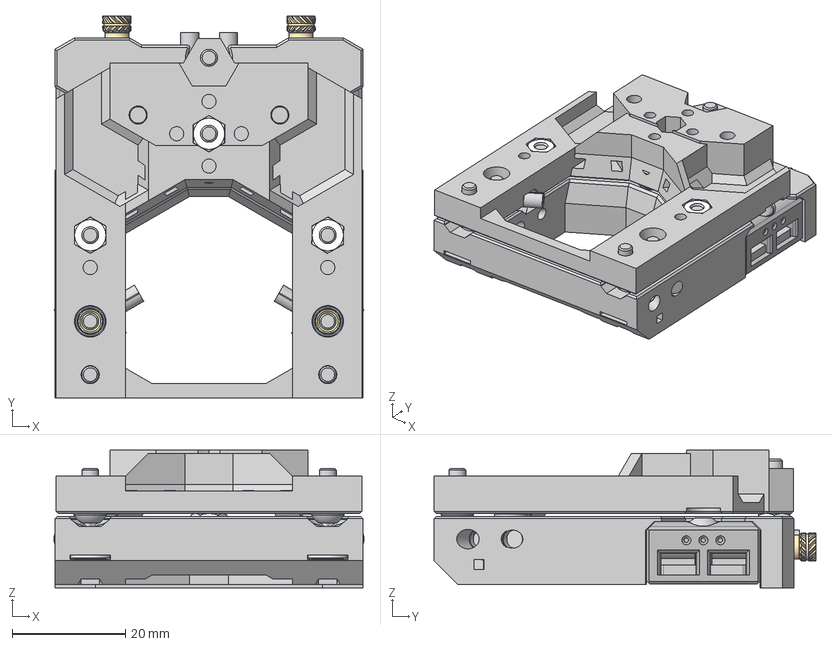
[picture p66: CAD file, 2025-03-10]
CAD/MadMax_Core_MGN9H_DB_AH_v11.step
54.7 x 67.4 x 24.3 mm
Magnet (4)
Magnet (2)
Magnet x 7
Magnet (3)
Magnet (1)
Magnet (10)
Pin (5)
Pin (2)
Pin (3)
Pin (4)
Pin (1)
Pin
M3x8 FHCS x 5
M3x35 BHCS
M3_Hexnut x 9
M3 Shim Washer x 2
M3x8 FHCS_1
Long Nut x 2
Clip x 2
Tube x 2
M3x10 BHCS x 2
M3 Threaded Insert v3 (3) x 2
Plate
M3x12 BHCS
M3 Threaded Insert x 4
M3x8 BHCS x 4
Crimp Terminal
Crimp Terminal_1
M3 Jam Nut x 2
M3x8 BHCS_1
M3x6 FHCS x 3

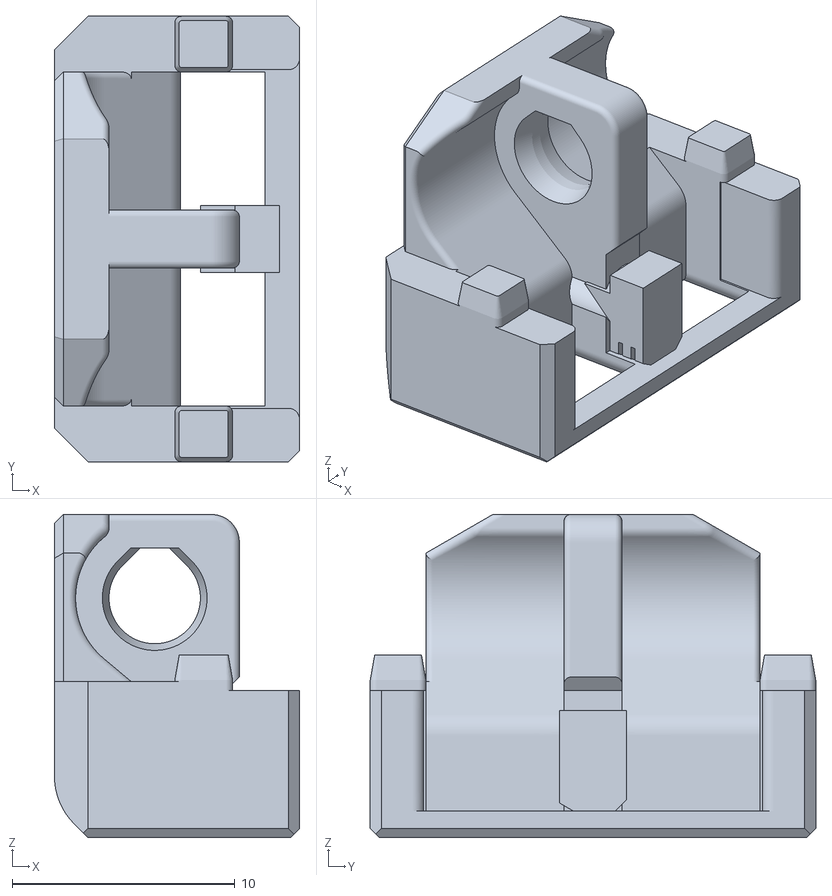
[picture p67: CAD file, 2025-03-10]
STL/SpeedClip_3mm_Gap.stl
11.0 x 20.0 x 14.5

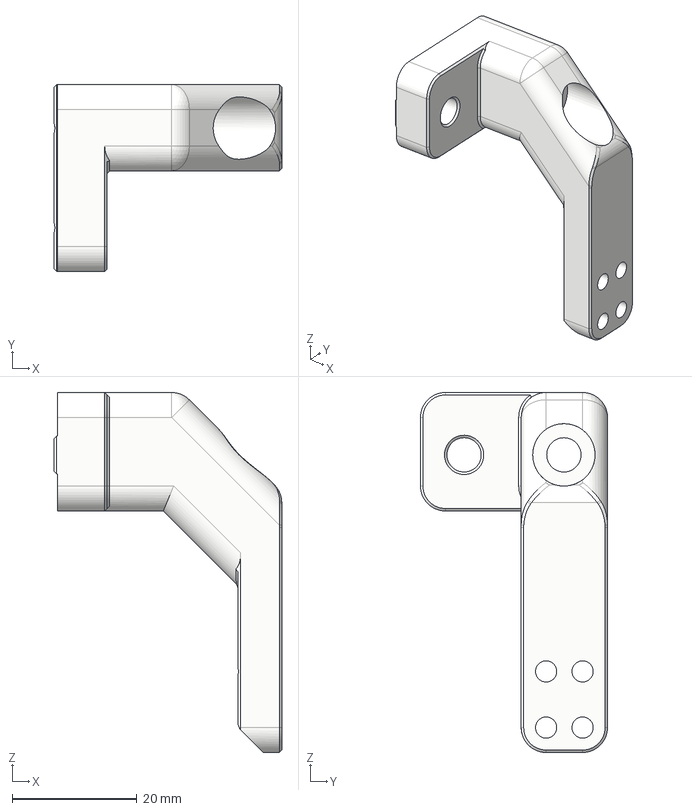
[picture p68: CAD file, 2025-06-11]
User Mods/andrewmcgr/XOL-A4T-Cartographer/CAD/Dock Arm.step
36.5 x 30.0 x 57.7 mm

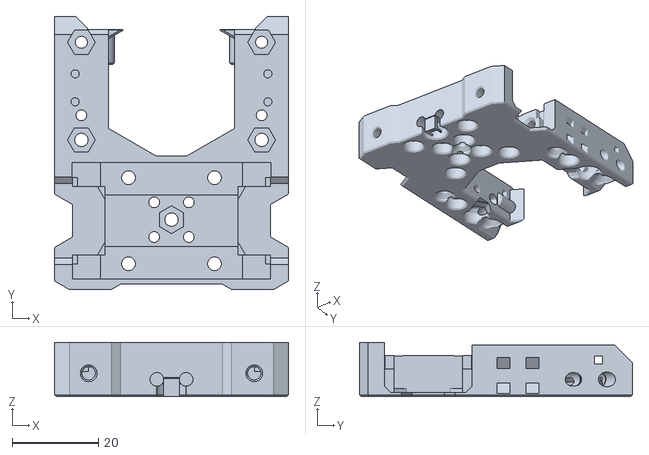
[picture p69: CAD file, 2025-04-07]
User Mods/andrewmcgr/XOL-A4T-Cartographer/STL/MadMaxCarriage.stl
54.4 x 63.5 x 12.6

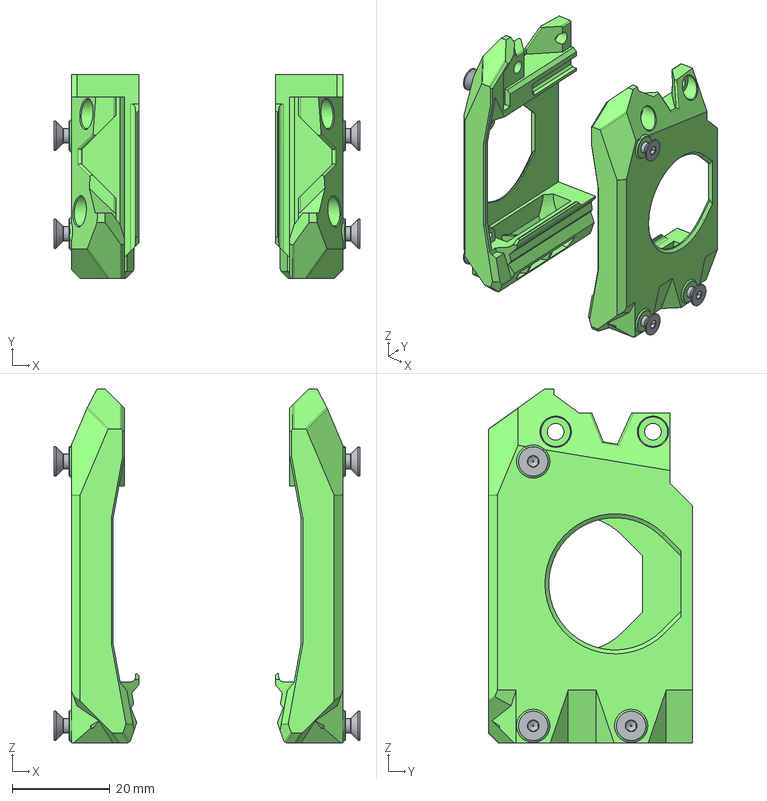
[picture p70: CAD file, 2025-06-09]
User Mods/joseph_greiner/ant_head/CAD/ant_head_ducts-std.step
62.4 x 41.6 x 72.3 mm
left_duct_std_mm001
M3x8-Screw004
M3x8-Screw005
M3x8-Screw006
M3x8-Screw
M3x8-Screw001
M3x8-Screw002
right_duct_std_mm004

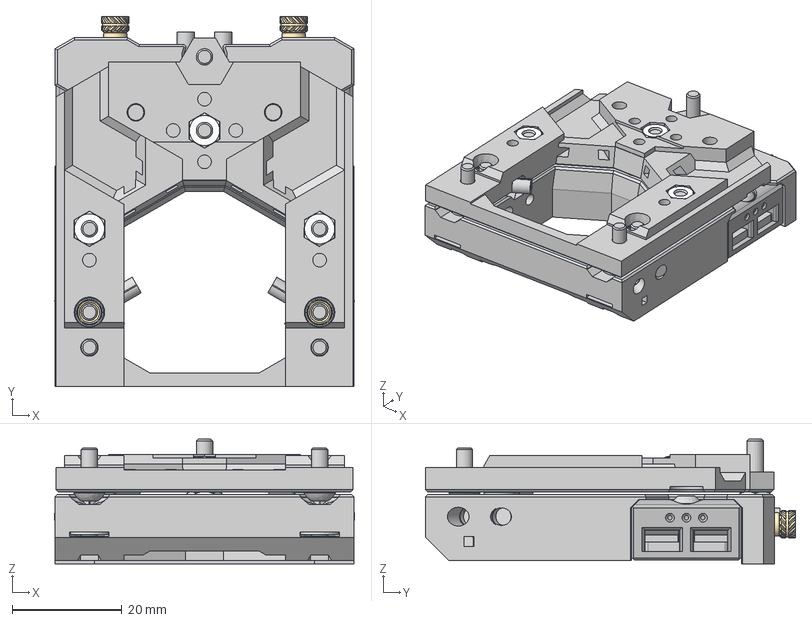
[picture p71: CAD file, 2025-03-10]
CAD/MadMax_Core_MGN9H_MSB_v11.step
54.7 x 67.4 x 22.7 mm
Magnet (4)
Magnet (2)
Magnet x 7
Magnet (3)
Magnet (1)
Magnet (10)
Pin (5)
Pin (2)
Pin (3)
Pin (4)
Pin (1)
Pin
M3x8 FHCS x 5
M3x35 BHCS
M3_Hexnut x 9
M3 Shim Washer x 2
M3x8 FHCS_1
Long Nut x 2
Clip x 2
Tube x 2
M3x10 BHCS x 2
M3 Threaded Insert v3 (3) x 2
Plate
M3x12 BHCS
M3 Threaded Insert x 4
M3x8 BHCS x 4
Crimp Terminal
Crimp Terminal_1
M3 Jam Nut x 2
M3x8 BHCS_1
M3x6 FHCS x 3

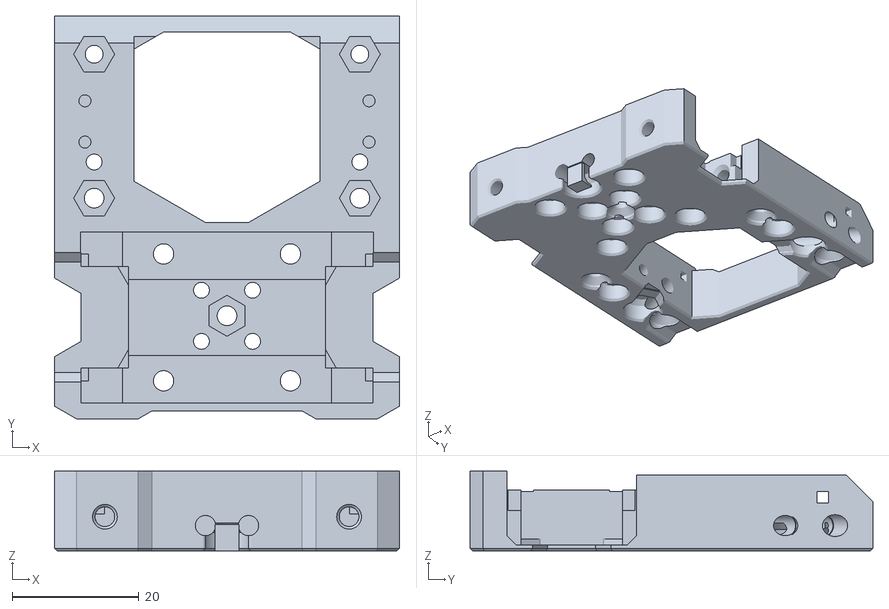
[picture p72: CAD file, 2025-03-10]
STL/Carriage_MGN12H.stl
54.4 x 63.5 x 12.6

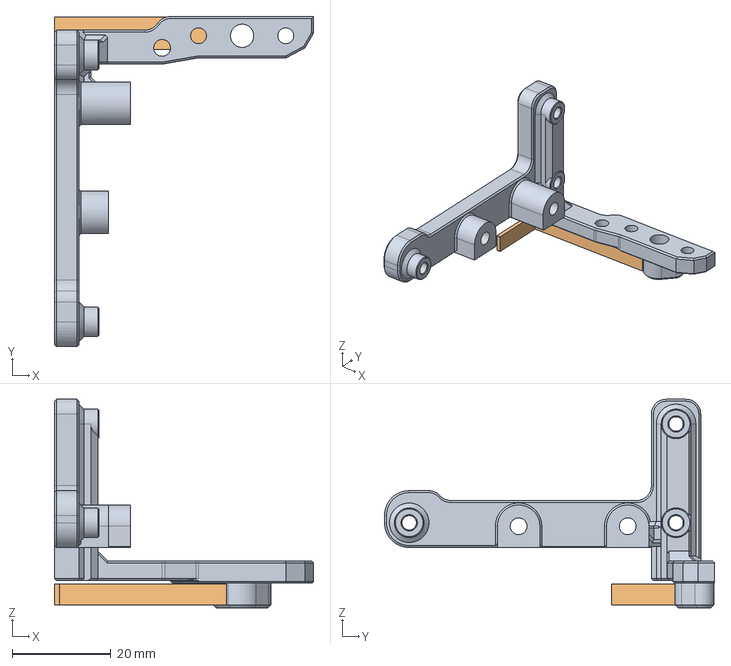
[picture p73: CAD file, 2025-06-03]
User Mods/andrewmcgr/XOL-A4T-Cartographer/CAD/Alternate Bracket.step
52.5 x 66.8 x 42.2 mm

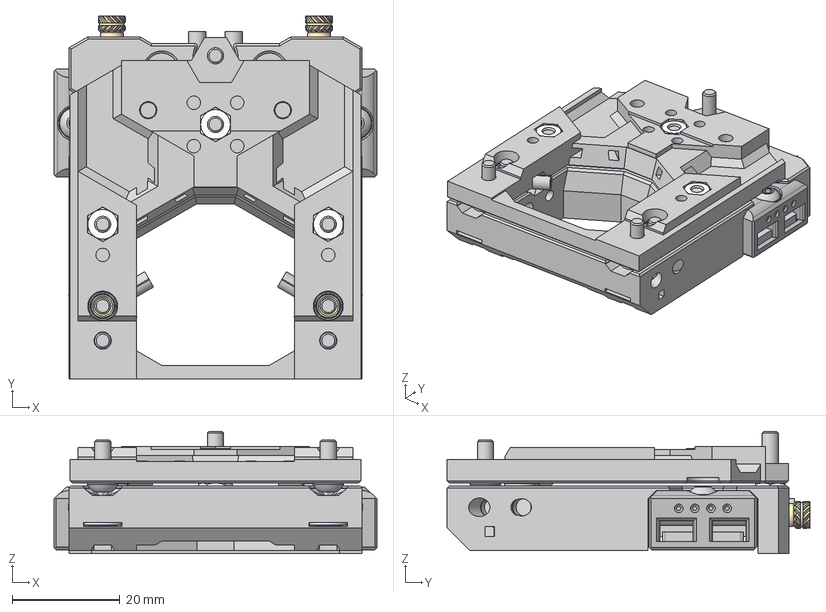
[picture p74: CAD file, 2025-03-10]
CAD/MadMax_Core_MGN12H_MSB_v11.step
60.0 x 67.4 x 22.7 mm
Magnet (4)
Magnet (2)
Magnet x 7
Magnet (3)
Magnet (1)
Magnet (10)
Pin (5)
Pin (2)
Pin (3)
Pin (4)
Pin (1)
Pin
M3x8 FHCS x 5
M3x35 BHCS
M3_Hexnut x 9
M3 Shim Washer x 2
M3x8 FHCS_1
Long Nut x 2
Clip x 2
Tube x 2
M3x10 BHCS x 2
M3 Threaded Insert v3 (3) x 2
Plate
M3x12 BHCS
M3 Threaded Insert x 4
M3x8 BHCS x 4
Crimp Terminal
Crimp Terminal_1
M3 Jam Nut x 2
M3x8 BHCS_1
M3x6 FHCS x 3

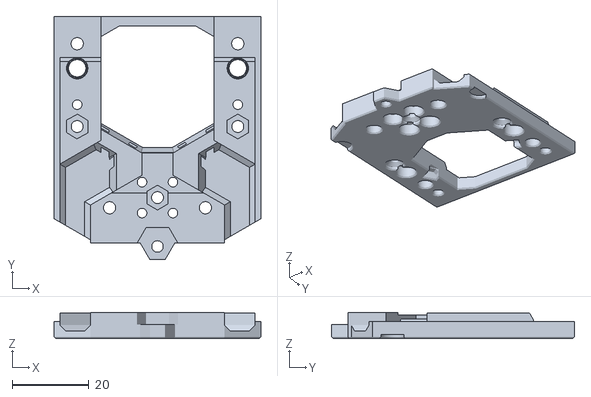
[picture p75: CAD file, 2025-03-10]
STL/Plate_MGN12H_MSB.stl
54.0 x 63.4 x 6.80

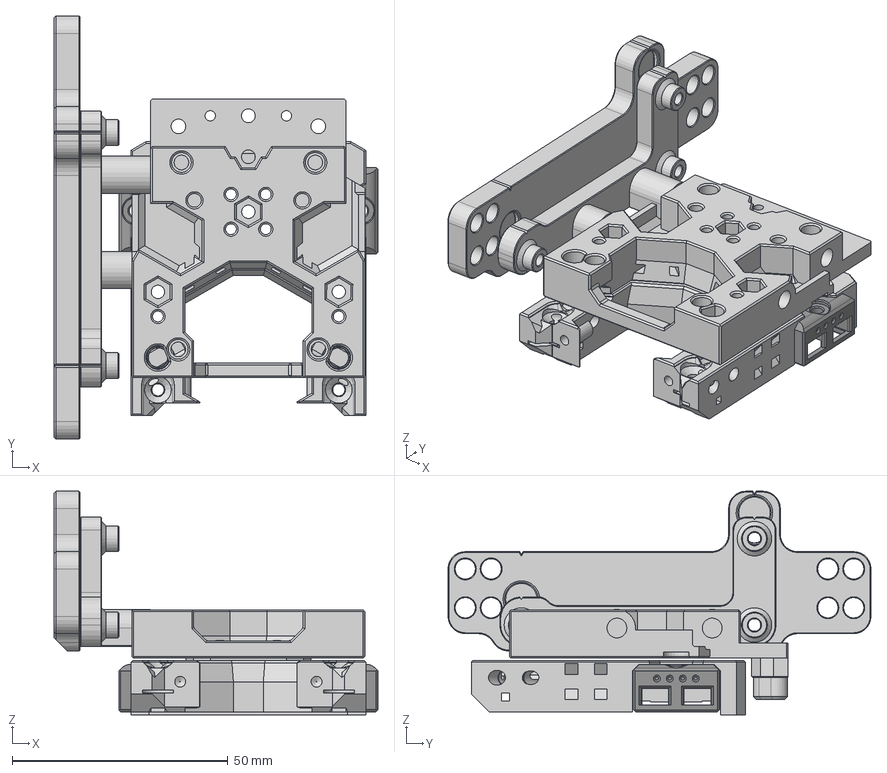
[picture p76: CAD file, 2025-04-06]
User Mods/andrewmcgr/XOL-A4T-Cartographer/CAD/MadMax 4 XOL v11.step
75.0 x 98.0 x 51.8 mm
Clip x 2
Plate
Plate Back
Dock Bracket
Dock Asembly

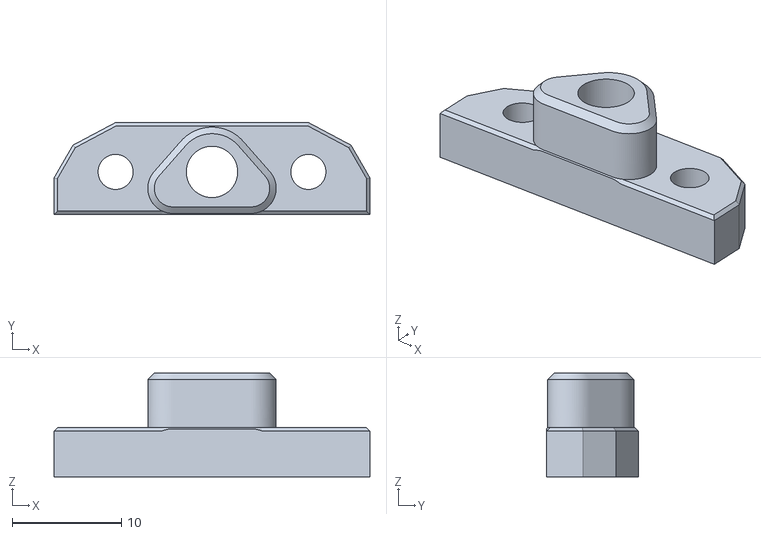
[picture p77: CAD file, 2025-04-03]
User Mods/andrewmcgr/XOL-A4T-Cartographer/STL/Plate Back.stl
28.9 x 8.42 x 9.50

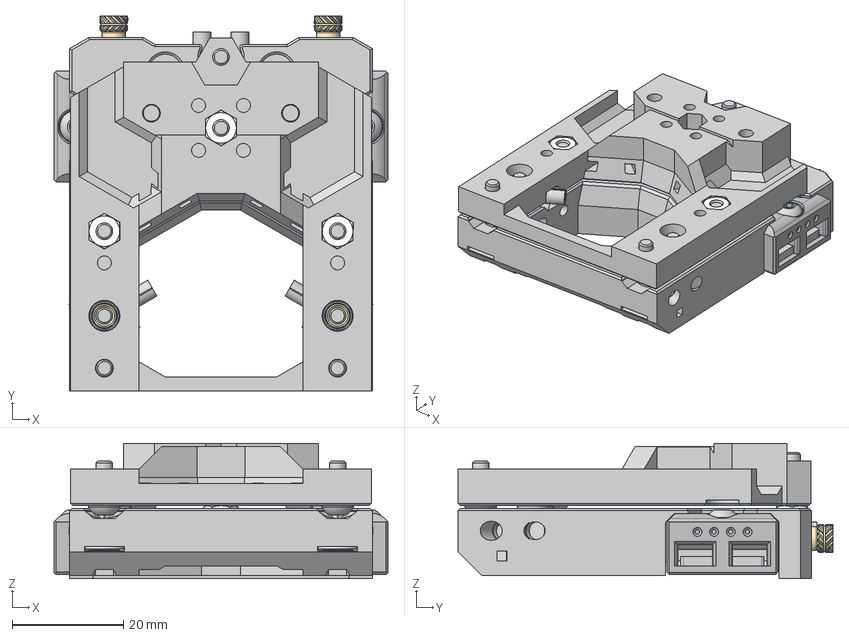
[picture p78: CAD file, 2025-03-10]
CAD/MadMax_Core_MGN12H_DB_AH_v11.step
60.0 x 67.4 x 24.3 mm
Magnet (4)
Magnet (2)
Magnet x 7
Magnet (3)
Magnet (1)
Magnet (10)
Pin (5)
Pin (2)
Pin (3)
Pin (4)
Pin (1)
Pin
M3x8 FHCS x 5
M3x35 BHCS
M3_Hexnut x 9
M3 Shim Washer x 2
M3x8 FHCS_1
Long Nut x 2
Clip x 2
Tube x 2
M3x10 BHCS x 2
M3 Threaded Insert v3 (3) x 2
Plate
M3x12 BHCS
M3 Threaded Insert x 4
M3x8 BHCS x 4
Crimp Terminal
Crimp Terminal_1
M3 Jam Nut x 2
M3x8 BHCS_1
M3x6 FHCS x 3

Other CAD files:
User Mods/wulfsta/XOL-A4T-MGN9/CAD/MadMax_4_XOL_Plate_MGN9.step
STL/Plate_MGN12H_DB_AH.stl
User Mods/andrewmcgr/XOL-A4T-Cartographer/STL/Dock Bracket.stl
STL/Test_Print.stl
CAD/SpeedClip_Configured_v39.f3z
STL/Carriage_MGN12H_9mm.stl
STL/Carriage_MGN9H.stl
STL/Plate_MGN9H_DB_AH.stl
STL/Plate_MGN9H_MSB.stl
STL/SpeedClip_4mm_Gap.stl
STL/SpeedClip_4mm_Gap_9mm.stl
User Mods/andrewmcgr/XOL-A4T-Cartographer/STL/Alternate Bracket.stl
User Mods/andrewmcgr/XOL-A4T-Cartographer/STL/Dock Arm.stl
User Mods/andrewmcgr/XOL-A4T-Cartographer/STL/Dock Asembly.stl
User Mods/joseph_greiner/ant_head/STL/ant_head_ducts-std.stl

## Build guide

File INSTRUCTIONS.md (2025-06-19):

## INSTRUCTIONS.md

**Follow the instructions here to ensure a high-quality build.**

Sure, you can just look at the CAD and BOM and ignore the instructions (or any build videos).

But please… don’t do that. There are some non-typical techniques used here, like reaming holes to match pins, plus intentionally overtorquing screws to match-fit holes.  

Order matters, too.  The fastest approach is to build the carriage and plate, then test them together first, then put them on the printer and actually print with them.  

Only then, should you proceed to the dock-side hardware and other software configuration.  Breaking the steps into smaller testable pieces, with intermediate milestones, tends to keep builds on track.  

You can do it!

If you experience issues, check the [Troubleshooting](TROUBLESHOOTING.md) page first.

### Print Settings

Regular Voron **toolhead** considerations (materials and printing) apply here, as critical parts are millimeters away from a heated bed.  They will be subjected to high heat, and you want them as resilient as possible.

**Settings:** All parts will print at stock Voron settings (0.4mm nozzle, 0.2mm layer height, 4+ walls, 5 top/bottom, 40%), but more perimeters, top/bottom layers, and more infill will help ensure rigidity.  You want these parts strong, so print extra extra hot, in a hot chamber.  The bridges are short, anyway!

**Material:** ABS works fine to print PLA in unenclosed systems, but in an enclosure, especially a well-insulated one, the carriage and plate see high temps, so use a more temperature- and creep-resistant plastic if you can.  ASA is recommended over ABS, but PC or PC-ABS are even better.

**Test Print:** A `Test_Print.stl` is included; print this part to confirm your sizing first.  The magnet should press in with force, the FHCS should snap into place, the heatset should fit securely, and the part should be at the right height.

**Parts:** Print all parts matching your carriage size and toolhead type. Typical printing:
* 1x Carriage
* 2x Plates
* 2x Belt Clips
* 2x Docks
* 2x Toolhead parts (cowling, extruder, TH board mount, ...)

The no-brace MGN9 plate is for Dragon heatblocks, to add clearance.

For all docks and toolhead parts, check with the provider.

**Tools:**
The following tools are required for a complete build:
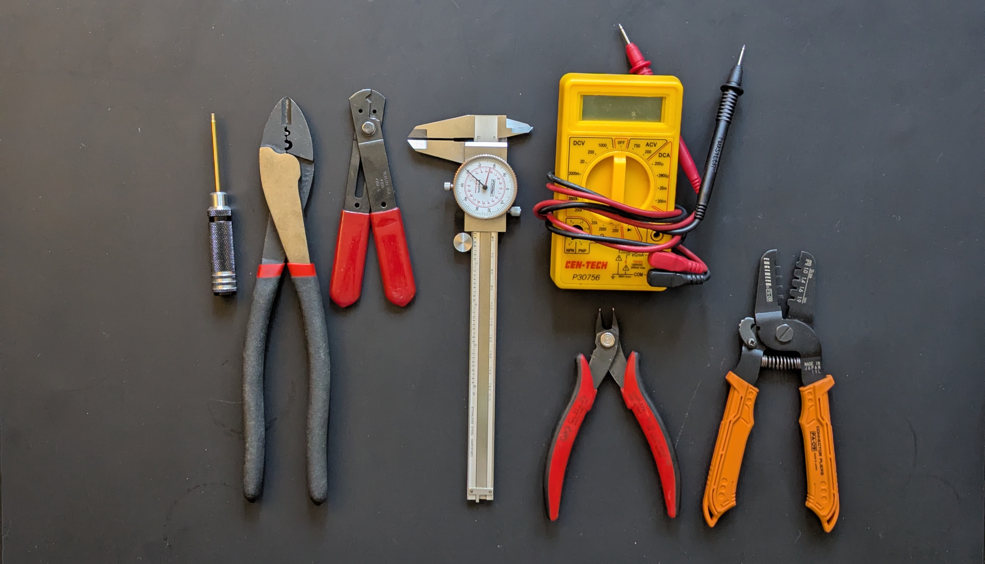
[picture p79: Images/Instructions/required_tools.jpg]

* 2mm straight hex driver (not balldriver) - for M3 BHCS
* Crimp tool - for ring terminals
* Wire stripper
* Calipers
* Multimeter
* Flush cutters
* Wire cutters

Optional tools, but recommended:
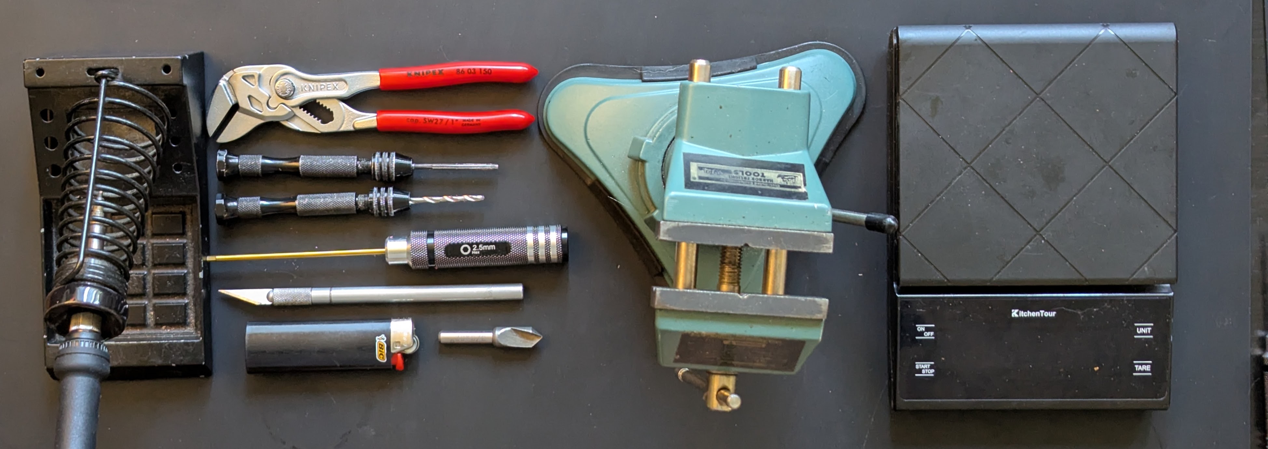
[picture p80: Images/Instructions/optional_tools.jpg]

* (If homing with endstop switch)
  * Soldering iron
  * Lighter or heat gun for heatshrink
* Pliers Wrench (Knipex 180mm+ length preferred) - for magnet insertion
* 3mm Reamer [Amazon](https://www.amazon.com/dp/B07K49B4LC)
* 1/8" Reamer [Amazon](https://www.amazon.com/dp/B07JPDSSBM)
* Holder for reamer and hand drills [Amazon](https://www.amazon.com/dp/B07TRGW3W7)
* 2.9mm drill bit
* 2.5mm straight hex driver (not balldriver) - for M3 SHCS
* X-acto knife
* Countersink - for part cleaning
* Bench vise
* Scale for measuring probe force [Amazon](https://www.amazon.com/dp/B08SM4TB8P)

### Carriage
Build the carriage first, so you can match both plates to it.

|  |  |
| --- | --- |
| Front | Rear |

Parts needed:

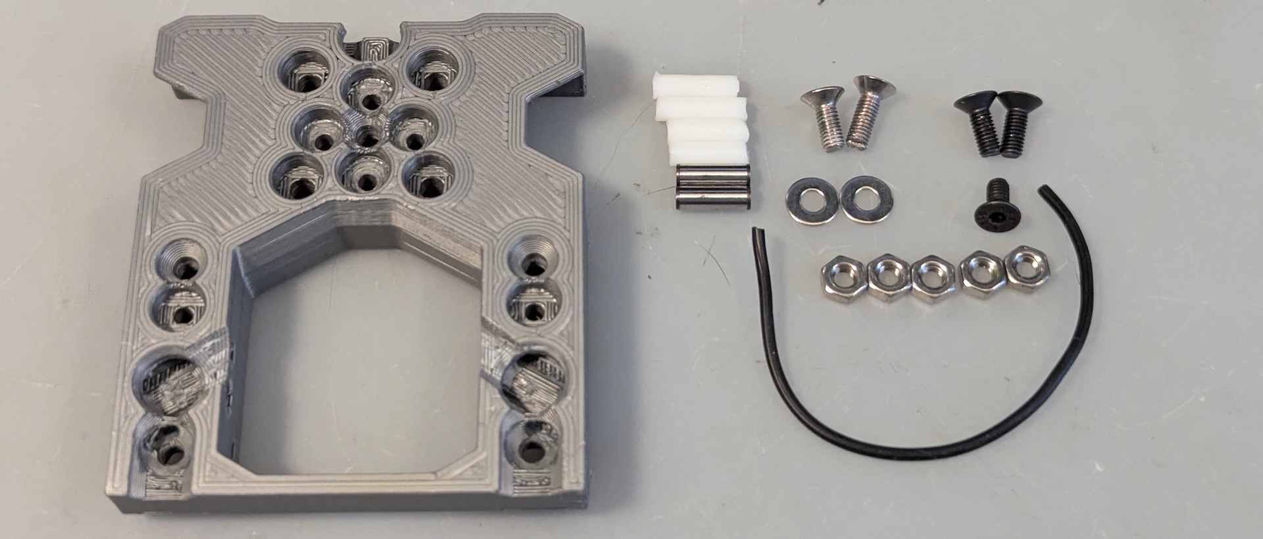
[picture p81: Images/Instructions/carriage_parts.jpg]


There are two types of FHCS used here: magnet-retention screws up top (3x, stainless or alloy), plus electrical-connection screws below (2x, must be stainless).
* Tips
  * Create a “nut push tool”: an M3x8 SHCS plus M3 nut, twisted into a spare M3 T-nut.  Later - adjust the depth to ensure nuts get pushed-in fully to the plastic part!  
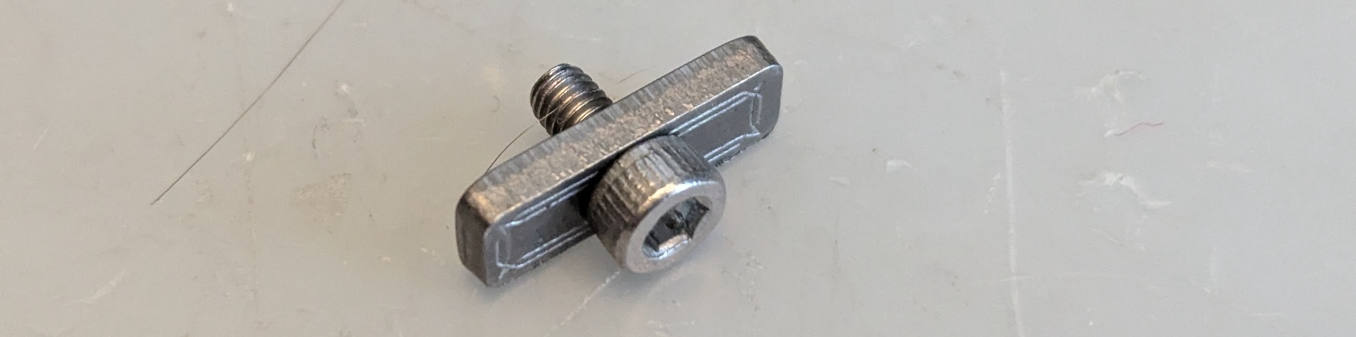
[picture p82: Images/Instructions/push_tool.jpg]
   
  * If magnets don’t fit, likely because the print is overextruded, use a 6mm drill bit or reamer plus spot of glue.
  * Magnet removal: All magnets can be removed from the backside by pushing hard with the short side of an allen wrench, like this:
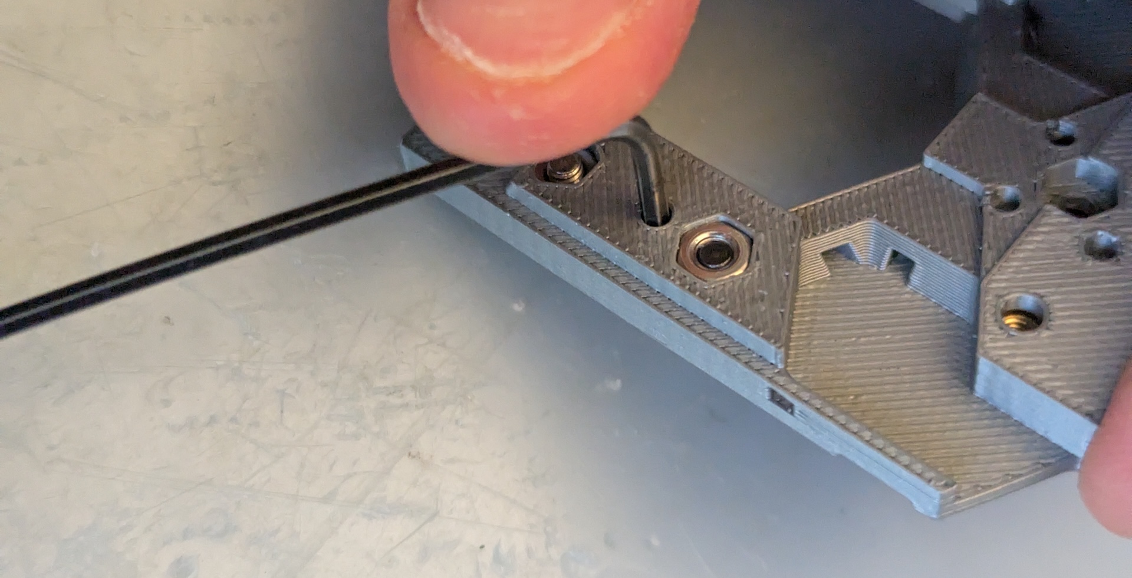
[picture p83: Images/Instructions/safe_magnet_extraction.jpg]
 
* Prep
  * Clear any elephant foot for magnet holes with a countersink bit.
  * Clear out the 4x carriage-mount holes with a 3mm reamer or drill bit.
  * ⚠️Measure your pin diameters with calipers.  You want holes right at the measured size, with whatever drill bit or reamer you have.
    * Plastic can have some slight dimensional variation here.  Steel pins should be spot-on.
  * Clear out the 2 top holes for the belt-clip pins with a reamer.  Test it with a pin; you should have a loose slip fit, where the pin inserts and removes easily.  Tension and gravity will hold it securely in place.
  * ⚠️GENTLY clean all 6x pin holes with a reamer, to avoid the carriage splitting between layers when you add the pins.  A light twist is probably more than enough.
  * Make plastic pins (4x)
    * Typically 9-10mm is a good length for these.  To cut acetal, DON’T use a tube cutter, as you may destroy it!  Use something stronger, like thick wire cutters or flush cutters.  Mark a length with a Sharpie, then cut to length, then trim the ends for easier insertion.
  * Remove the insulation on the ring terminals: use flush cutters to cut the insulation on the open end to get a grippable tab, then put an allen key through the ring, and pull with pliers (gripping hard!) on the tab.  It should come right off.
  * (Endstop-switch-based homing option only - recommended)
    * Cut two 60mm wires and strip one end of each.
    * Solder and heatshrink both wires to the switch.
  * (Sensorless homing option only)
    * Cut and strip both ends on one 60mm wire.
* Add pins
  * ⚠️Be super gentle, to avoid layer separation.  If you’re experiencing resistance, push out the pin, then ream out the hole slightly more.
  * Metal pins (2x)
    * The metal pins are the two lowermost ones on the carriage, which complete the circuit.
    * Press pins until fully inserted, from the outside, until they just touch the inner “leg” edge.  Start with fingers, then push to fully inserted by pressing against a flat surface.
  * Plastic pins (4x)
    * Press the two middle-height pins in, from the outside, until you can't see the ends.
    * Press the two upper pins in, from the top down, until they hit the stops.
      * Yes, the top ones stick out intentionally, for easy removal with flush cutters.  
    * All other 4 lower pins can be removed later using an allen wrench, pushing in on the holes.
* Add magnets
  * ⚠️Decide how many, and which type, of toolhead magnets to use.  The toolhead weight, carriage size, and probing type affect the choice.
    * Always balance the magnets around an FHCS, so it doesn’t twist out.  Don’t use 3 magnets; always use 2 or 4.  Use a weak 3rd + 4th magnet for balance, or just use 2.
    * Lighter toolheads may be OK with weaker grip; for example, 2x N52 for a 280g toolhead.
    * Heavier toolheads (350g+) will need more magnetic force for a solid toolhead grip; typically 3x N52, minimum.
    * Be careful to get the polarities right!  You want neighboring magnets to have opposing polarities, for more grip.
  * Push the magnets (toolhead + lower 2) to where they hold in place, then use a pliers wrench, small vise, or body weight and a flat surface, push.  If pressing with fingers, find a slightly larger-dia magnet or other surface to prevent going in too far (say, 8mm dia magnet).  They should press-fit flush without issue, then hold without anything else.
* Add upper nuts
  * Fully insert the 3x nuts that will secure the magnet-retention FHCSes.
* Add magnet-retention FHCSes
  * Add 3x magnet-retention FHCSes; tighten until the FHCS heads are flush.  Yes, you’ll apply a lot of force here, and the magnet will move down slightly.  To check flush-ness, use a rigid PCB ruler if you have one.
* (Sensored homing only)
  * The orientation of the switch (plunger up, or plunger down?) will depend on the printer type.
  * Secure the endstop switch with two M2 self-tapping screws; fully tighten them, but be careful not to overtighten.
* Add electrical-wire connections
  * Slip an M3 shim in from the bottom.
  * Push a shiny metal FHCS through the washer, so the washer stays in place.
  * Push wire into place.  No wire insulation should overlap the washer and nut.  You want a solid connection, so try to bend the wire around the screw before the nut comes in.
  * Add nut and push down (using push tool), then tighten screw fully.
  * Pull wire hard, to confirm connection quality.
  * Repeat for the other side; trim and restrip if desired.
* Test
  * Using a multimeter, ensure an electrical connection from Maxwell metal pin to metal pin.  You should see near-zero resistance.

### Plate

|  |  |
| --- | --- |
| Front | Rear |

Parts needed:

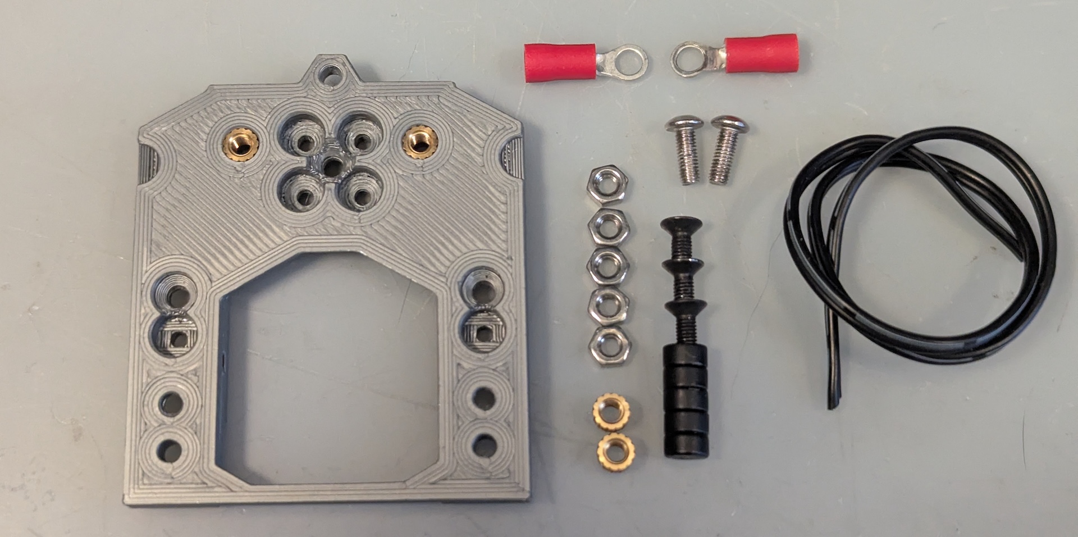
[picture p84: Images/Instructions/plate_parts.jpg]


* Prep
  * Clear any elephant foot for magnet holes with a countersink bit.
  * Match-fit the upper Maxwell coupling screw hole by overtorquing with an M3 screw, then remove it.
  * Setup the 3 Maxwell BHCSes:
    * For the upper, use an M3 nut, typically 2.2-2.4mm in thickness; measure what you have first.  Using pliers and a straight allen wrench, lock the nut to the end of the button head.  The screw length will depend on your toolhead choice.
    * You want to match the thickness of the two lower maxwell screw assemblies to the upper.  Measure the thickness of your crimp terminals (typically 0.3mm to 0.8mm) and use either jam nuts (typically 1.8mm thick) or stacked 6mm-OD 3mm-ID washers to get as close as possible to 2.2mm thick, but not lower, and as matched as possible.  0.2mm mismatch is OK; the docks and the printer will be fine with a tiny bit of misalignment.
  * Heat-press the 2x heatsets for the toolhead screws and ensure they’re flush.
  * Heat-press the 2x heatsets for the Maxwell coupling, through the print-bed side.  Despite being the "wrong way" to resist pullout, pullout forces are low here, and the orientation means more of the heatset will be in contact with the crimp terminals, for a better electrical connection.
* Add magnets
  * In this step, you'll use the carriage to ensure the correct polarity of magnets on the plate.
  * Add one magnet to the carriage.
  * Push the plate into the carriage, so this magnet is mostly inserted.
  * Repeat with all remaining magnets.
  * Fully insert all magnets until flush, using a pliers wrench, small vise, or against a flat surface.
* Continue, following the same steps as the carriage:
  * Add magnet-retention-FHCS nuts (3x)
  * Add magnet-retention FHCSes (3x)
* Feed wire into position
  * Figure out which side you want the wires to go, remembering that the plate will be flipped.
  * Trim one wire side slightly shorter, and feed it straight down, through the vertical slot, to where it can enter the screw/nut area.
  * Route the other end of the wire through the 3 tunnels.  Adjust the length of the short or long wire to match; both should just touch the bottom brace.
  * Strip both wire ends 6-8mm, or whatever length works best for your crimp terminals.  Need more length?  Pull it through.   Excess may be taken up at the toolhead.
* Add electrical-wire connections
  * Using the crimp tool, crimp the ring terminals to the wires.
  * Put the crimps in place, with the thick part facing into the cutout, and for each, add the M3x8 BHCS-nut assembly and fully tighten.
  * Strip the upper ends a few mm - just enough to connect to the multimeter.
* Test
  * Put the plate on the carriage, gently.  DO NOT let them click hard into place.  You can damage the soft screw heads.
  * Look at area between plate and carriage, from the side, with a light source behind.  You should see a fraction of a millimeter, all over.  All FHCS heads and magnets should be flush.  If you can see the screw heads or magnets popping out even slighty, fix them to be flush, to avoid hard-to-diagnose issues from rubs.
  * Using a multimeter, touch the lower Maxwell screw heads, confirm that the toolhead + plate combo has continuity in the default position and doesn’t when you press up gently on the plate.
  * The “Maxwell coupling switch” here should have a discrete, clicky feel, and return into position reliably.  If it’s mushy, you need to find the rub and fix it, or find the loose part.
* Lockdown
  * ⚠️Threadlocker on ALL 3 Maxwell screws is a smart choice - Yeri and Zruncho have both experienced issues from screws loosening over time, from probing and attach/detach motions.  Add it.
* Repeat steps above for each plate.

### Pins and Belt Clips

|  |  |
| --- | --- |
| Front | Rear |

Parts needed:

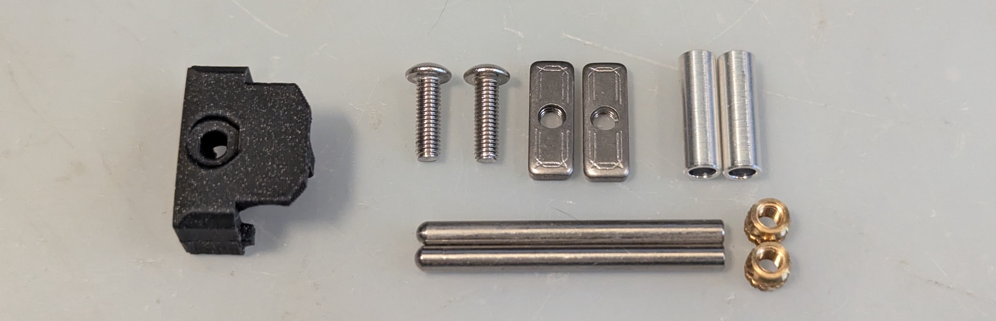
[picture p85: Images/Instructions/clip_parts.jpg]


**Pins**
* Drill out 2x M3 heatsets using a 2.9mm or similar drill.  Get close to 2.95mm or so, and leave a small taper on the narrow side.
* Using a small tabletop vice or pliers wrench, press heatsets into the flat end of 3mmx35 pins.  The wide end should align to the pin end, and be flush.

**Belt Clips**

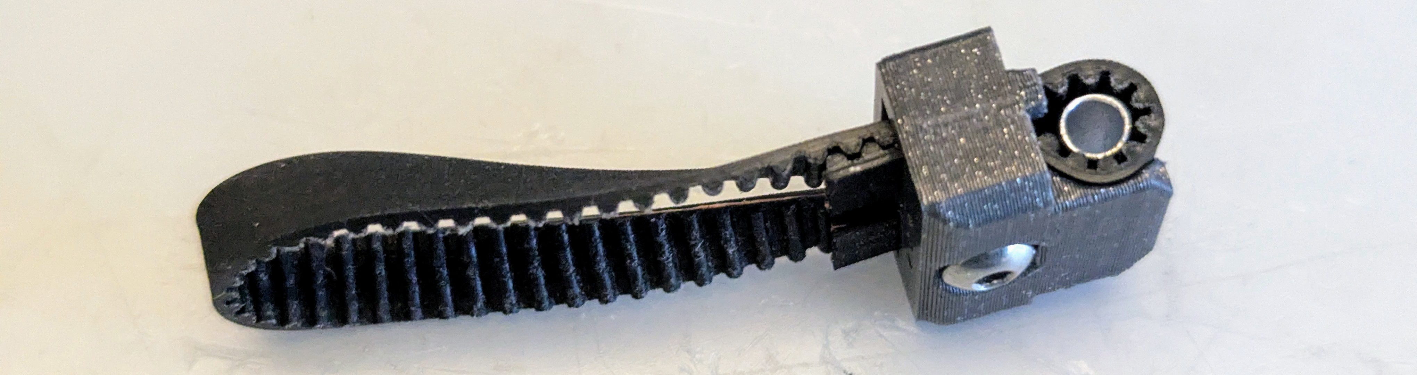
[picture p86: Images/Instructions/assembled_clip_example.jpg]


* Prep
  * Remove the tiny custom support for each belt clip, near the screw hole.  Clear the support area with an x-acto or flush cutters, if needed; you need the M3 t-nut to fit here.
* Add M3 t-nut in place and then add M3 BHCS, keeping it as open as possible, but still holding the t-nut with at least two threads.
* Practice Install
  * Before going to your printer, get the feel for belt installation, with a piece of spare belt.
  * Feed the spare belt through the entrance with the teeth facing the front and fold it back on itself (where the teeth face each other) and push it through.
  * Adjust the positioning, a belt tooth at a time, to where maybe 2 teeth are exposed beyond the clip.
  * Drop the tube in, halfway, so it holds in place from the belt squeeze.
  * Repeat for the second belt, then press the tube in fully.  Make sure they exactly match; if off by one tooth, you'll see a 1mm error where one belt tooth is half-shifted to the opposite side.
  * Fully tighten the M3 screw.
  * Push clip into carriage and press the pin down.  It should drop in with minimal-to-no force.
  * Repeat for other clip, for more practice.
  * Adding belt clips with tubes goes fast, once you get the hang of it!  SpeedClips can be adjusted in-place, which makes the initial setting faster.  It's how they got their name.
  * Tip: to have fast belt-clip reattachments or initial settings, using a metallic silver Sharpie, mark the first visible tooth on the long (continuing) belt side.  Measure the number of teeth and use it as a reference for other belt ends; mark those to match, and it goes FAST.
* Real Install
  * Loosen the screw and ditch the practice belts, and repeat on the printer.  We’re doing this live.  Get excited!

BEFORE messing with docks and toolchanging and all that config, get the damn thing printing and test the build quality!

You now have a lighter-weight, lower-cost Tap replacement that enables painless nozzle swaps and maintenance.  You should only need to:
* Add crimp terminals and a crimp terminal housing to the plate for the toolhead board
* Update a pin in your Klipper config for the probe
* Add the carriage and clips to the printer
* Add grease to the metal pins for better longevity

Then you can test probing functionality, probe accuracy, and get updated resonace-testing results.  All those will confirm that you have a good build.

What to expect:
* Homing with the probe should just work, with some visible carriage motion.
* The coupling should return to the connected position, reliably.  If it doesn't, you have too much friction or crappy magnets.
* `PROBE_ACCURACY`: run with SAMPLES=100 to work it in.  Ignore what you're looking at; the grease and parts need to settle.
  * Then do SAMPLES=10 and expect sub-0.01mm range and lower standard deviation (sub-.002mm).
* `Z_TILT_ADUST` or `QUAD_GANTRY_LEVEL` should work fine, next.
* Resonance testing should be clean, and possibly much better than before; the head should be well-balanced and rigidly connected.  It took a lot of work to shift the head downward to improve balance and improve cooling flow.

Before printing, make sure to update the Z offset for yur toolhead head... the offset will depend on your printer and the magnet configuration, but 0.4mm is a reasonable starting point.

### Toolhead and Docks

Most MadMax toolheads use 3 or 4 M3 FHCSes sticking out from the front, which slide into a dock, and are held by magnets, along with standard keyhole geometry.

For each toolhead, add your 3-4x FHCSes, and measure the distance from the flat screw top to the flat toolhead surface with the tip of calipers. The magnets in the dock should be about 3mm inward from the flat surface, and you want to match this distance to maximize magnet grip.

For each dock, add 3x-4x magnets from back, until they hit the lip, partially.  

Check with your dock maker for any other instructions.

BTW, you can add just one toolhead and test out docking and undocking if you’d like. You don’t actually need more than a shroud with a hotend and a toolhead plate to be connected; you can always add a plate extension cord to the mainboard, before setting up the toolhead board, to play.

Continue to the [Configuration](CONFIGURATION.md) section next!

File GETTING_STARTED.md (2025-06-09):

## Getting Started

Step one is to choose the options for your printer.  Top questions are in this section; many options are tied together, so the safest approach is generally to use a complete setup known to work, like one of the first beta builds.

**Printer Type?** Good news everyone! Many printers with a front-facing X rail and XY-motion-head will *potentially* work.

Static-gantry and flying-gantry CoreXY and Cross-XY printers are game, but not bed slingers - because Y motion is needed to detach the head, and you don't want to be slinging your other tool around on the bed.  

**Main printer?**
Yes, the conversion can be on your main printer, surprisingly.  The carriage/plate design is robust and reliable, after 100s of hours of beta-program testing and many design iterations.  You can even just use the core as a probing-capable or easy-detach head, try it out, and then decide if you want to add a second head and docks.

**Change Frame?** Travel loss will depend on the configuration.  Square static-gantry printers necessarily lose the front corners when using both extruders.  If you want to enlarge the frame, consider whether to go wide, deep, or tall; all can work, though a tall setup with frame-mount docks will take longer for toolchanges and be harder to tune as a result.  The picture below gives a sense of this space loss, with a simple and probably overly optimistic loss of 54mm wide x 57mm deep, for a range of common bed sizes.

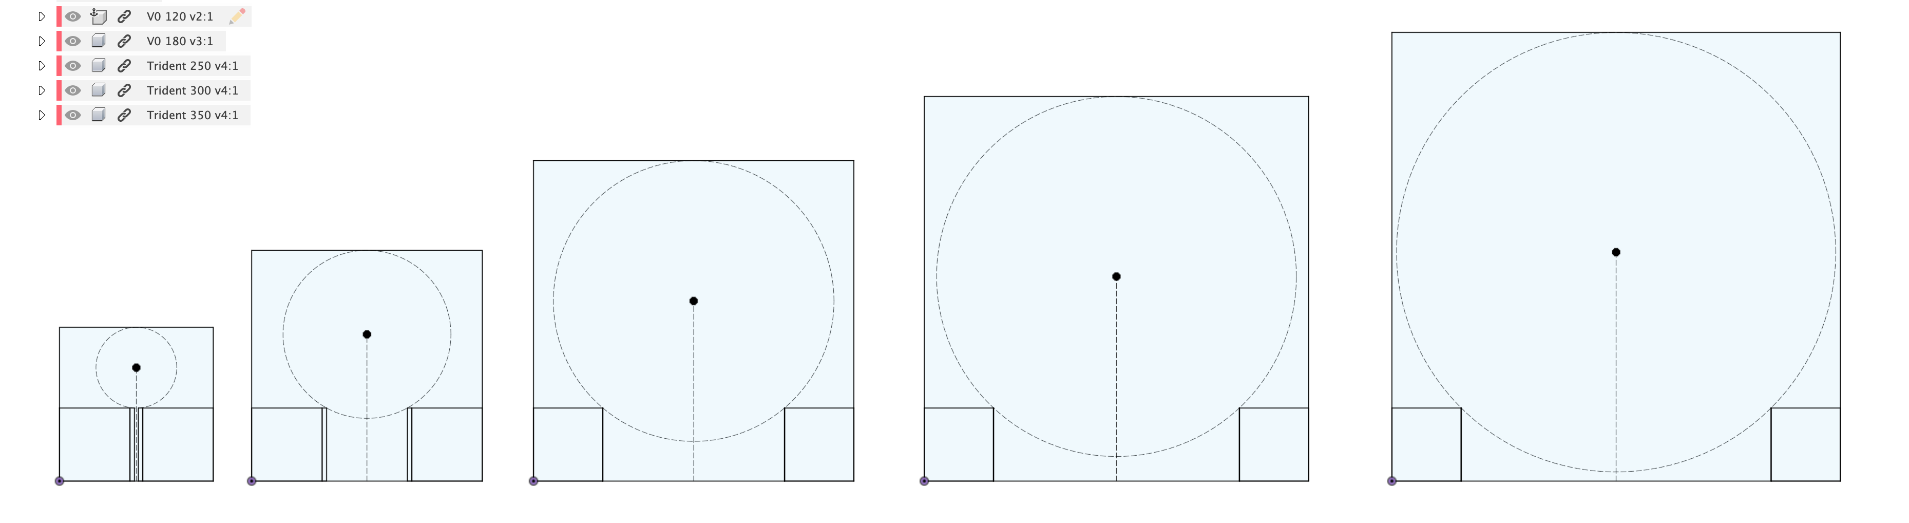
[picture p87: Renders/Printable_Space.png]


Expanding your frame is premature optimization, if you don't have a driving use case.  You can always build this with what you have, then make that larger financial and time decision, later.  It's not just the cost to expand the frame and buy panels and longer rails, it's the time to remount and replace parts too.

Remember though, that this loss is almost entirely in two-extruder mode.  With a single extruder, you don't lose the front corners, though you may lose a little bed of bed from doing a bed Y shift.  Speaking of which...

**Shift the bed?** If your frame has no overtravel, you need a bed shift in Y to avoid the inactive nozzle touching your bed - either melting the build plate, or preventing bed leveling.  On some printers, like Trident, there is built-in overtravel which helps clear the nozzles, as well as give space to use something like a Nudge probe too.  Some methods to achieve a Y shift include:
* Adding bed-shift mounts to a bedframe, like the Tri-Zero bed mounts - or removing them and direct-mounting to an extrusion (like Zruncho did for MM.000)!
* Modifying front Z attachments to shift the bedframe pivots
* Doing nothing; if the MadMax core shifts your head forward already, no additional motion may be needed
* Moving the printer front forward, with a fridge-door mod, to create clearance for the front shift.

**Which dock type?**
Docks come in a few flavors:
* Null - probing only, as a Tap or Boop replacement
* Gantry-attached: only XY motion needed to dock/undock; the most likely choice here, but less convenient for more than 2 heads.
  * "Stalagmite" - sticks up, like Ambrosia's Trident docks
  * Slip-over - wraps around idlers, above and below, like Yeri's Salad Fork docks
  * Idler-attached/integrated - connects to, or replaces, front idlers; more compact, but harder to evolve
  * Monolithic - provides idler base, box that connects to a frame, like Zruncho's T0 docks
  * "Stalagtite" - hangs down, as seen on Zruncho's Dueling Zero prototype docks.
* Frame-attached: Z motions required, similar to Tapchanger/Stealthchanger docks, and for flying gantries only.
  * Many of the above design may work just fine, as long as they have added clearance for the flying gantry.

With the exception of Zruncho's T0 docks, which only fit OmniBrick, all the others keep the same dock-FHCS spacing as DragonBrick's original docks: 20mm Y spacing, 54mm Z spacing.  You still need a dock that matches your chosen head's offset, too.

**Which toolhead/extruder?** Fortunately, you have choice!  

See below for ones that use the MadMax reference design - a square of holes for FHCSes, where those screws are in parallel plane to the printer's sides, with keyslots to hold the head using the FHCSes and magnets to keep them in place, even when the umbilical pulls backwards and the head weight wants to twist the head forward.

Note that MGN9H vs MGN12H MadMax core parts, as well as different belt sizes and spacings, are not compatible, however many toolheads use compatible parts (assuming the same rail size, belt size, and belt spacing).

## Select a toolhead/extruder combo

Either you pick a toolhead which is (1) already compatible with the Mini Stealthburner 3-hole pattern - DragonBurner, Dragon, OmniBurner, AntHead, etc. - (2) already compatible with Xol-carriage like Andrewmcgr's A4T/Xol plate - or (3) modify the MadMax plate to support your current toolhead of choice.

There are lots of known-good choices here, many “brickified” - that is, with:
* front-top-mount square toolhead boards
* slab sides to hold the dock screws

A few of the supported heads: A4T, AntHead, OmniBrick, DragonBrick:

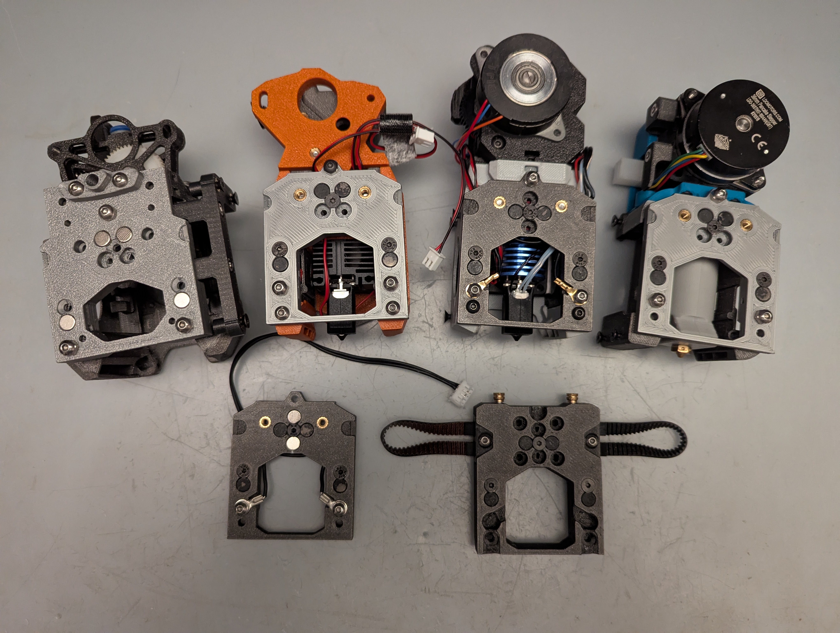
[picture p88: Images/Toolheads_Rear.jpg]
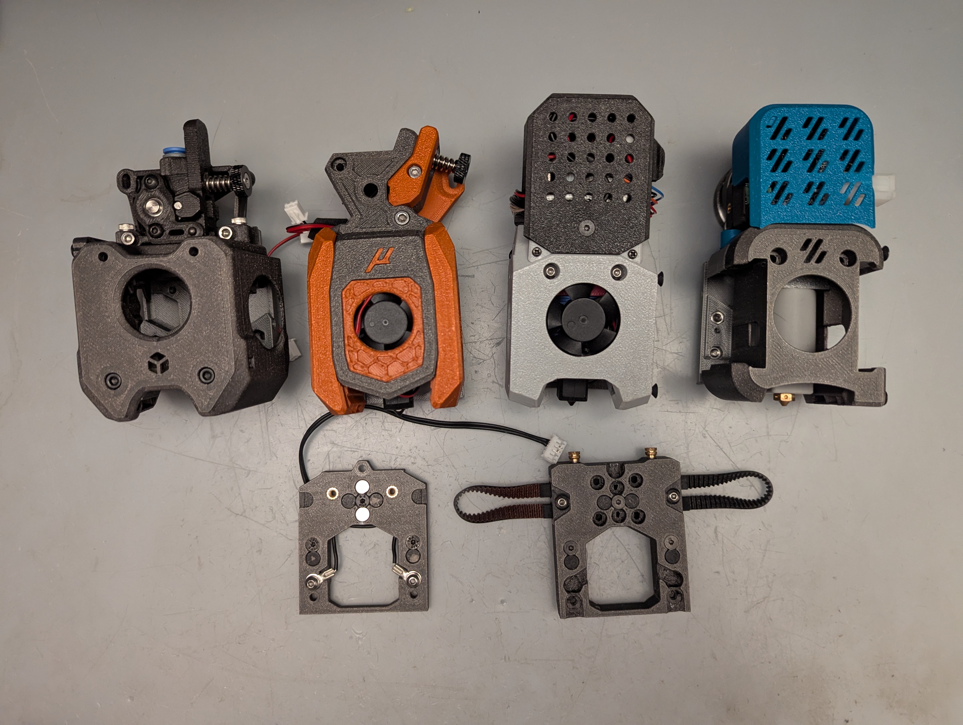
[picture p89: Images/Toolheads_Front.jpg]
|  |  |
| --- | --- |

A brickified toolhead is not a requirement, but it’s a good fit for any MadMax printer.  Why?  By moving the toolhead board from the back to the front, you reduce the chance of one head hitting the rear of the other, which typically frees up Y travel (up to 20mm).  This increase is meaningful with MadMax conversions, especially at the smaller Printers for Ants scale: more Y travel means more usable print volume for two-extruder prints.  Beyond that, the toolhead board mount can be more rigid, can potentially yield more useful input shaper measurements, and moves wires away from the Maxwell coupling, so they can’t catch and break.

Brickified toolheads tend to be harder to make when there’s a large shaft in front (G2E) or when the filament drive gears are fairly wide (Bondtech style).  Newer thinner-gear extruders (HGX2.0, LGXL2, K1), or extruders that don’t stick out much beyond the filament path (PapLite), tend to be more popular with MadMax conversions.

### DragonBrick/RapidBrick, by Rob

The DragonBurner and RapidBurner are toolheads by Chirpy, which are super-narrow (54mm wide), have wide extruder support, and have good cooling from 40mm fans.  They use a 3010 hotend fan.

Rob developed DragonBrick and DragonBurner based on these, with modifications for toolchanging using MadMax docks, plus matching extruder mods with a square front toolhead-board mount and cover to keep the wires tidy.  This is a surprisingly narrow and compact-in-depth setup, especially with the K1 extruder mod.

The full list of modifications include:
* Reshaping the front Cowl for more rigid air ducts
* Squaring off one side of the ducts and working in holes for FHCS screws for docking
* Custom extruder mount for a Modified K1 Extruder
* Modified K1 Extruder face place for EBB42 mounting
* Custom electronics shroud
* Other small QoL changes.

As a mod, these toolheads accept available Dragon Burner and Rapid Burner hotend mounts.

A .step file is provided for the entire brick version of the toolhead, which is designed around a modified K1 extruder and EBB42 board.
 * K1 Extruder parts links:
   * AliExpress
     * [Extruder body](https://www.aliexpress.us/item/3256804562096106.html), $20.50
     * [Motor, 10-tooth](https://www.aliexpress.us/item/3256805685028416.html), $14
   * Amazon
     * [Extruder Body](https://www.amazon.com/Creality-Extruder-Upgraded-Extrusion-Mechanism/dp/B0CJV1L2XG), $20.30

### A4T/XOL, by andrewmcgr

The A4T is a solid option, intended for longer, higher-flow hotends, with dual 40mm fans, a 2510 hotend fan, and CFD flow optimization for strong cooling.

Unlike other toolhead options, andrewmcgr added support for the A4T and XOL by modifying the MadMax plate to have its own L-shaped piece to hold the dock screws, instead of modifying the *toolhead itself* to add those.  It sounds like it will be flimsy, but feels and is plenty strong in practice.  Plus, there is no need to port toolhead changes in the future.  Both toolhead options share the same modified plate.

There is an optional modified MGN12H carriage which adds Beacon/Cartographer support, provided by this mod, too.

It retains full X travel in toolchange model; either head can reach the full width of the bed, except for the forbidden areas around the docks.

Andrew says: "Combined with full Y for some of the bed, and it reduces the bed area by less than 15%... though it does mean (with the docks done this way) that you don't get the full diagonal length. Doing extrusion-mount docks would allow for putting them all over one side and keep access to the diagonal, though at that point it also makes sense to build an extended-Y printer with extra overtravel.   Just for size reference... 5x4 gridfinity case fits with a ton of spare room... or all the skirt parts for a 350 Trident at once."

### A4TBrick, by Telxoid

A very different approach to andrewmcgr's, and more like the others: this mods the toolhead cowling to add screw holes for the dock screws.  

It also includes a modified PapLite front plate with holes for a square 42mm toolhead board, as well as a toolhead board cover, which somewhat "brickifies" the A4T.

This option uses Andrewmcgr's plate mod, but ignores the side-L-plate mount.

### Anthead Mod, by r2pdx

[AntHead](https://github.com/PrintersForAnts/AntHead/tree/main) is hartk’s latest toolhead design, which also uses 2x 4010 and 1x 2510 hotend fans.  It's cleanly integrated, hides some wires, and looks good.  Its extruders generally have a third screw on the rear which more solidly locks them to the cowling, and it's only slightly wider at ~55mm than the 54mm DragonBrick.

r2pdx on Discord is Joseph Greiner on GitHub, and whoever they are, they've made it easier to use the AntHead by modifying the cowling to support the usual MadMax dock screws.

This choice uses the same parts as the DragonBrick option; they add a bit of Y distance, but share the usual MiniSB 3-hole mounting.

### OmniBrick, by Zruncho

OmniBrick exists to give more space needed to use Nudge with a V0, plus enable the use of a PapLite extruder with a third mounting screw, for added stability and better resonance-testing results.

OmniBrick is based on [OmniBurner](https://www.printables.com/model/854317-omniburner-universial-mini-stealthburner-for-most) - Kevin’s “fits all extruders” chopped MiniSB derivative.

OmniBrick is Zruncho’s de-stealthed OmniBurner derivative (via copious face deletions), which has front Huvud and EBB42 support with a PapLite, plus two rear heatset holes.  You can use pretty much any extruder, but the PapLite fits well with a square front toolhead board.

The Papilio Lite (PapLite) is Kevinakasam’s compact, strong belt extruder.  A belt extruder provides high grip and won't grind filament, at the cost of some extra weight.  It has a short distance from filament entrance to front plate, which makes a front toolhead board possible.   NOTE - pictures show the newer slimmer [HGX2/TBG gear option](https://github.com/kevinakasam/Papilio-Belt-Extruder/tree/main/Papilio%20Lite/_Ignore/HGX2.0xTBG) which enables ~8mm more Y travel, but these gears are not available as of 2025-04-06. Instead, we recommend either the r3 version or the TheFPVGeek-modified TPU-capable version (on the Kevinakasam Discord).

See [notes in Kevin’s Discord](https://discord.com/channels/964441223169449984/1240233572464459776/1245649529563385856). Also, [build instructions exist](https://kevinakasam.com/papilio-lite-build-instructions/), but are outdated.

You don’t have to use a PapLite and the included front square-toolhead-board mount.  But then you’ll lose some Y where the toolhead board sticks back and would hit the front of the other toolhead.

### Yavoth

Supposedly a bit more solid and more tightly packaged.

If you already have it and like it, and you have a bit more travel though (PB, PB0, SF, …) it’s a fine option, especially to get started.

### Other choices

Stealthburner and Archetype are not currently supported, and may never be.

The main caveat is that the magnetic-only design is not optimized for heavier toolheads, and if you want the Maxwell probing as a bonus, then the additional magnet force needed to hold the heavier “full SB” head up means a higher amount of probe force.  PZ, Klicky, Beacon all get around that, and should work fine, so it's not a blocker, but you would be the first to try out a full size toolhead.

It’d be pretty cool though.

The "widebody" MiniSB with added side plates was part of beta1, and it fits and looks cool, but it's not ideal for a 120mm V0, because you can’t do a front-mount Nudge on a V0; it's just slightly too wide to leave the required amount of travel. OmniBrick and StealthBrick are good options that allow a perma-mounted Nudge.

## Decide on Homing Method

In theory, sensorless homing should be accurate to a full step, which should be more than accurate enough for our use. The docks allow a bit of imperfection while still being reliable.

But in practice, any tiny issue with your build can make it finicky, and turning can depend on friction, which depends on belt tension, which can change.

The easy and reliable solution is to install endstop switches. The X-endstop can be mounted to the carriage and wired in line with the maxwell-probe.  See the example below.

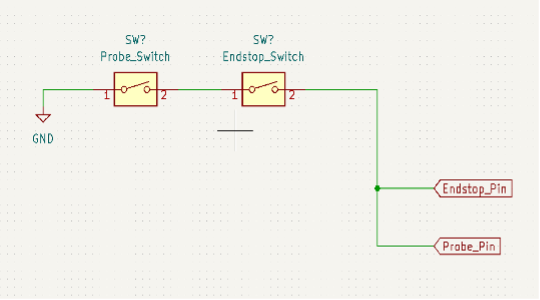
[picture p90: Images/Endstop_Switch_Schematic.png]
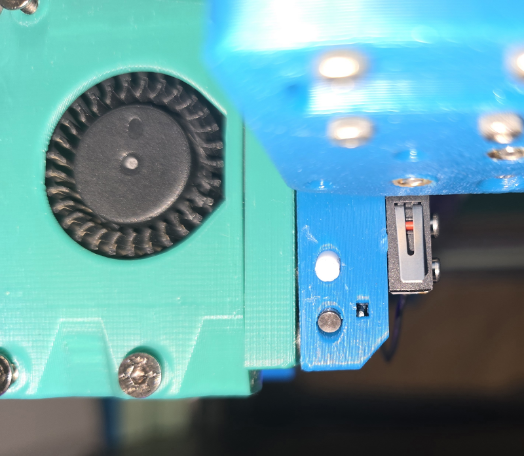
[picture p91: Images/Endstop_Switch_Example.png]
| |  |
| --- | --- |

Go for sensorless homing only if you’re 100% confident in your sensorless tuning, or if you’re willing to put a lot of time into getting there.

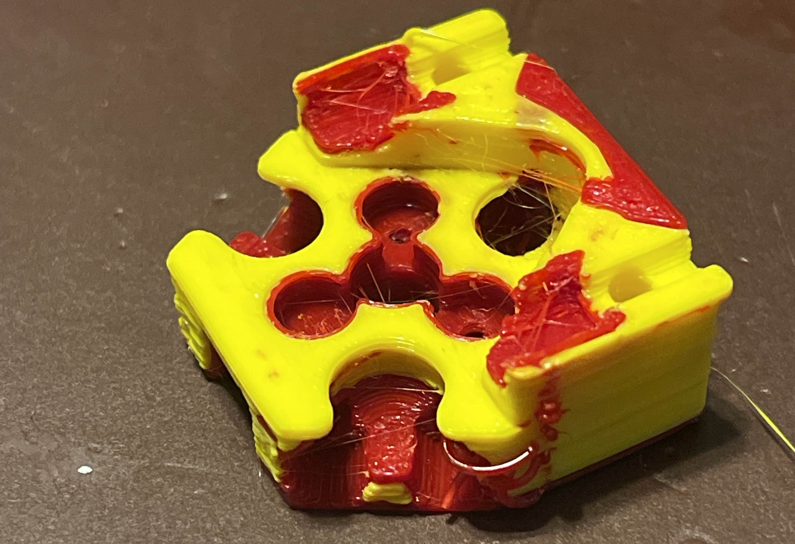
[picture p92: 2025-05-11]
Images/Builds/yeri_8_part_1920.jpg

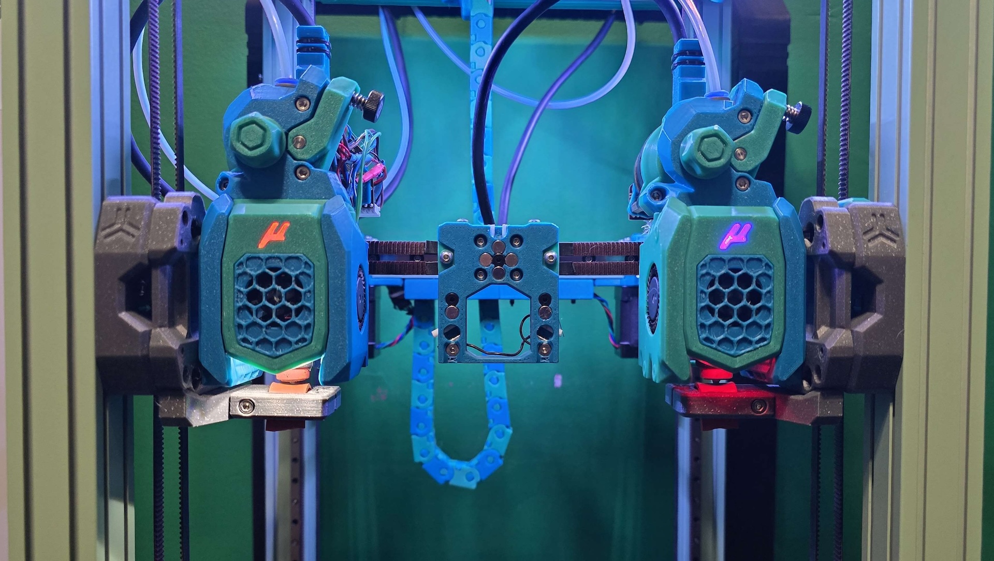
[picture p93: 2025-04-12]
Images/Builds/r2pdx_10_front_frame_mount_1920.jpeg

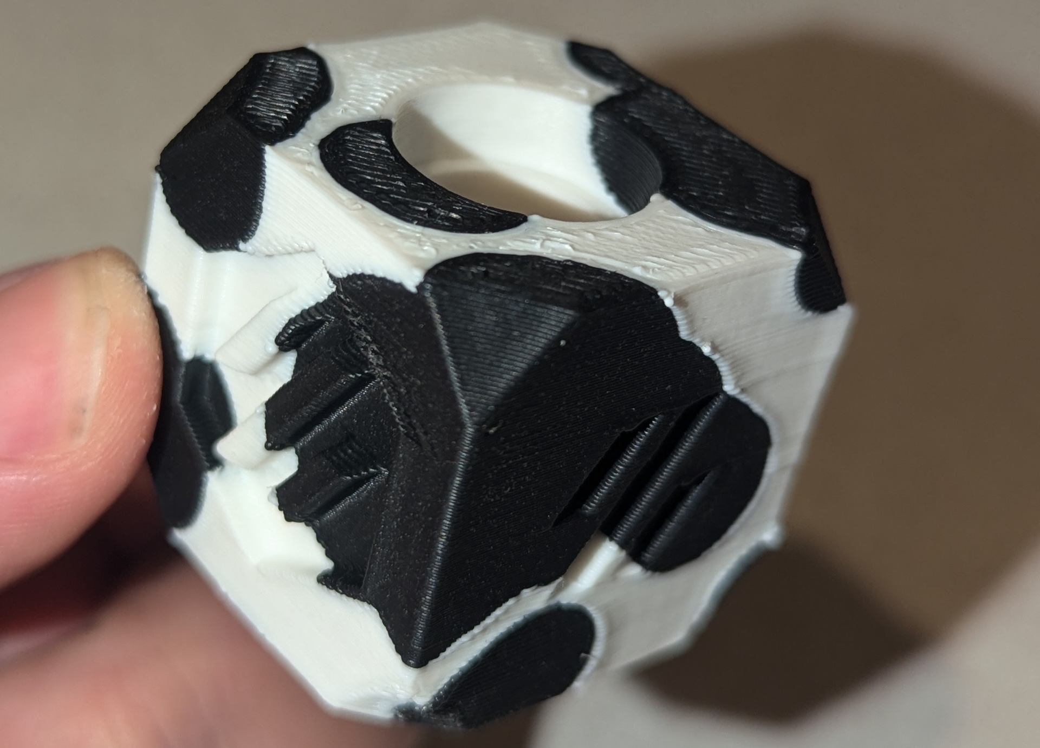
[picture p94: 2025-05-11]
Images/Builds/ambrosia_3_part_1920.jpg

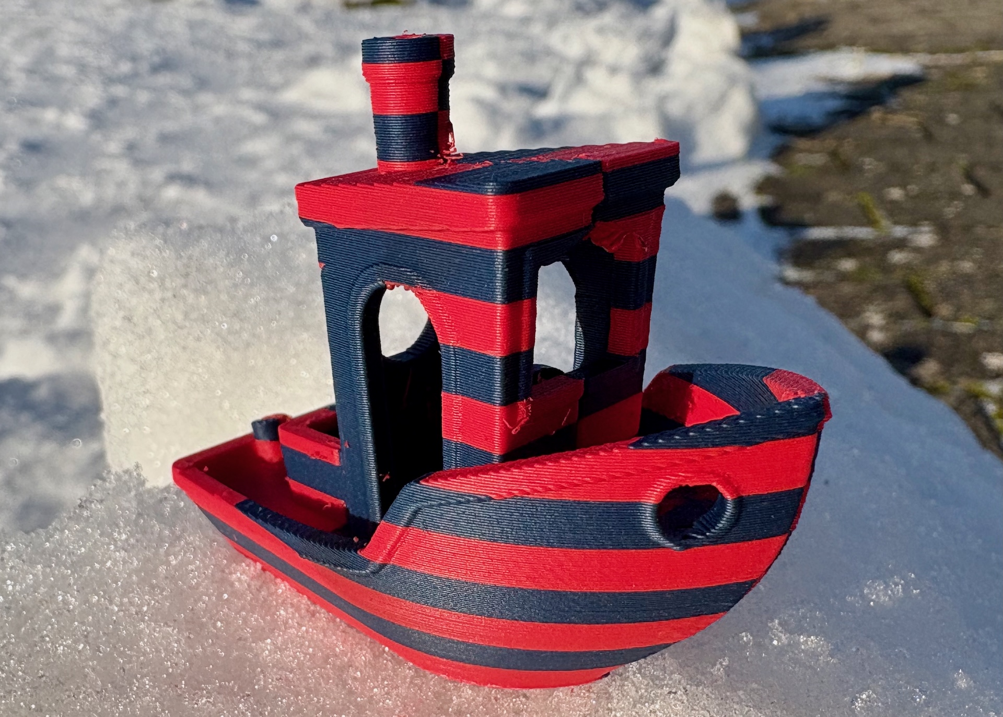
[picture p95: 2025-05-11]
Images/Builds/runningsystemchanger_5_part1_1920.jpeg

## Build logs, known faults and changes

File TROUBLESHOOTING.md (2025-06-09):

## Troubleshooting Notes

**NOTE: The top issue is fake N52 magnets.** Both the docks and the core require proper, full-strength N52 magnets. If you have not sourced from a known-good magnet seller, this is the most likely issue.  Random AliExpress stores may sell N35s as N52s.

### Failed docking and/or toolchanges

* Check for debris near the Maxwell coupling.
* Check for fully-seated magnets.
* Check that the FHCSes on the toolhead (which fit into the slots) are tuned to  the right length for the docks; they should just about touch the magnets, to maximize grip.
* If steppers miss steps during a print, all bets are off.  Make sure all speeds are well within a margin of safety.  [Autospeed by Anonoei](https://github.com/Anonoei/klipper_auto_speed/) is highly recommended to quantify your top-end speeds and accelerations; you can then derate to add confidence.
* Check homing quality.  Sensorless homing is not as trustworthy as sensored (endstop-based homing), and the variation may seem random.  While the core and docks are designed to support misalignment beyond 0.5mm in all directions, they can only tolerate so much.

### Magnets escaping
If magnets ever escape, for any reason:
* Ensure your magnet-retention FHCSes are large enough.  These should be at least 5.8mm diameter; 5.5mm diameter screw heads won't do anything.
* Or, the plastic is deforming and enabling the magnets to pop out.  Check for plastic deformation.  In the worst case of a hot chamber, your print material (if ABS or ASA) may not have the needed temp tolerance.

### Maxwell-probing failures
If seeing "Probe triggered prior to movement" errors:
* Ensure that the front of the bed is not more than 1.5mm above the rear; bed misalignment can causes unexpected effects that look like probe issues, when the bed is hit during the XY travel.
* Make sure the electrical contacts on the plate and carriage do not need tightening.
* Make sure the toolhead-board crimp terminals are fully inserted and reliable.  Marginal crimps + twisting to add them to a toolhead can trigger a wire failure here.
* Ensure that there is visible daylight between the core and plate; if a rub develops, it can prevent the electrical contact from closing.
* Make sure the magnets are proper N52, as noted above.

### Maxwell-probing variability

The toasty environment near the toolhead can cause issues which yield a reduction in probing quality, especially ZTA or QGL failures, especially with a sub-0.01 tolerance.  However, the cause can also be elsewhere, in a way that can *appear* like a core issue.

**When diagnosing probe variability issues, run through all the possibilities here.**  We've never had a case where it wasn't one of the items listed below.

* Carriage:
  * Ensure that there is no crud near the pins, and preemptively clean them... ABS seems to leave a film over time.  A quick buff of the button heads with ScotchBrite can help. For the pins, try a Q-Tip with alcohol cleaner, followed by a reapplication of grease, followed by a bunch of probe cycles to settle the grease.
  * Ensure that there is no play in the pins on the carriage.
  * Ensure that no cracks are present on the carriage, especially near magnets, pins, and screws.  Look in all directions.
  * Ensure that all magnets are still there (!).
  * Ensure that the SHCSes which attach to the carriage are fully tightened, and that they're not too long.
  * Ensure that there is visible daylight between the core and plate; if a rub develops, the rub can lead to variable quality.  You may see jumps in probing of 0.1mm or so, if the friction to return is too high.  
    * Check for deformed plastic near the magnets and magnet-retention screws.
    * Check for daylight near the top screw; if this screw gets progressively tightened over time, the gap can close near that screw, and create a hard-to-see rub.  This issue has only appeared on MiniSB toolhead derivatives (which use a thin plate), and not on DragonBurner derivatives (which have a much thicker plate to spread out the force of the top screw).
  * Ensure that the electrical-connection FHCSes and wire connection are tight. Measure the resistance of the electrical connection to ensure that it's not the issue.
* Plate:
  * Check that any toolhead-attachment (non-Maxwell) screws are fully tightened. These like to loosen with time and heat, due to proximity to the bed.
  * For MiniSB-derived heads, Check that the two MiniSB hotend-mount screws are tightened fully. These also like to loosen with time and heat.
  * Check that the 3 Maxwell screws are fully tight. The upper screw, in particular, likes to loosen with time, so threadlocker is highly recommended.
  * Check that the crimp connections to the toolhead board are solidly crimped, by pulling on them.
  * Check for any physical damage to the lower two Maxwell-coupling screws.  These appear to wear over time, because the software steel heads rub on the hardened steel pins, and as they flatten, the ability of the toolhead to center reduces.  In addition, force when the coupling is reattached may dent them slightly.
  * Check that the non-electrically-connected pins (the other 4) are not dented.  PTFE will deform with time, temp, and pressure.  That's why Acetal is the spec'ed material, as it is a harder-wearing, yet still low-friction material.  If these pins are dented, it will be harder to get reliable probing.
* Z motion:
  * Ensure that Z pulley setscrews are tight and secured with threadlocker.  The higher probe force of the MadMax coupling (up to ~1kg) has a habit of revealing issues in the Z motion side.  A way to get evidence for such an issue is to run `PROBE_ACCURACY` near each Z attachment.
  * Ensure that each Z belt is at appropriate tension.  If a belt slips and one side is weaker, this can yield a persistent probe offset or reduced repeatability.
* Other:
  * Electrical connections outside the core can become loose too, like a failed umbilical wire or bad crimp on the mainboard or toolhead board side.

**If all of these methods still lead to subpar probing (0.02mm StdDev or higher), then replace the two lower BHCSes.**  These are the closest thing to a consumable.  In a few cases, we've scratched our heads, and replacing the BHCSes immediately returns the probe to perfect (sub-0.001 Std Dev) results.  The good news: two screws are cheap.

### Nudge probing failures
* "Probe triggered prior to movement"
  * Look at the probe.  Is it touching, where it is?
    * It may need a bit more ‘spread’, or at least, a more accurate position for the given spread.  Sensorless homing variability can trigger this occasionally.
    * Not touching?
      * Probe triggered prior to movement - check resistance on Nudge; consider drift.
* Probe triggered partway through - add spread, to cover a different direction.
  * Also, make sure the head is not hitting front-motion physical limits, or losing steps from any motion.
* Other?  
  * Check wiring quality: ensure a reliable connection after many hits and in different places; could be from a failing umbilical or toolhead board cable.

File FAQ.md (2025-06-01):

### High-level comparisons

Q: How does this compare to other toolchanger options?

A: The main way this is unique is that the kinematic coupling uses XY motion only, and does not have a positive lock.  For comparisons to other open-source projects, keep reading.

Q: How is this different from TapChanger/Stealthchanger/MISSChanger?

A: These are key ways:
* Static gantry support, so you don’t need a flying gantry printer OR to make a liftbar, which reduces complexity.
  *	This attribute enables many printers to get a toolchanger addition: Trident, Salad Fork, V0, T0, etc.
  * As a result, toolchanges are faster, without having to go to 48V or do any optimization, because there’s no Z motion needed.
* The attachment mechanism differs; it doesn’t have a positive lock, only magnetic.
* The stock docks are different, and don't need Z motion; each toolhead has screws that mate to the docks.

Q: How is this different from Daksh?

A: Both are similar, in that they share the XY-only motion, but MadMax only has a magnetic coupling, vs a positive lock with a rolling pin for Daksh.  As a result, Daksh (like the Prusa XL on which its toolchanger mechanism derives) can withstand higher forces on the head, before a detach occurs.

Q: Why not just use an IDEX?

A: With an IDEX, you need at least one extra motor driver and Y moves are necessarily slower, since you have two toolheads’ worth of inertia to overcome.  

On any typical CoreXY printer, Y moves are harder than X moves, because the full X gantry weight must be overcome, which makes Y moves the input shaper bottleneck.  Making the bottleneck even worse is Generally Bad, and in this case, since Klipper only has a single combined X and Y axis max acceleration parameter, the whole machine is then likely to run slower as a result.

There’s also a second head stuck there when you don’t want it, which requires a larger frame or reduces travel, and makes a conversion harder; you rarely see stock-square printers with IDEX conversions, because you have no way to get that space back, even if all you want is a single-extruder print.

Q: Why not just use a Dual Gantry if you’re going to have two heads?

A: In comparison to dual gantry, a toolchanger can be an easier conversion, uses more off-the-shelf mods, is lower cost, uses any printer, has easier maintenance, results lower complexity, can use stock Klipper kins, … the list goes on.  That said, DG avoids the complexity/risk of a kinematic coupling, and has more toolhead choice as a result.
You can even mix the two, and try out MadMax in-place, on your D0.  Zruncho’s done this crazy thing - putting a toolchanger inside a deal gantry printer.  It’s all reversible and easily installed.  You can even keep all the wiring in place.

Q: Why not just use a magnetic IDEX here?

A: “Magnetic IDEX” - more accurately named Shared-Axis Toolchanger (SATC) - is a toolchanger, but with a shared axis, so you still incur the weight penalty of the second head on Y moves, yielding inferior print quality or slower speeds for the same quality. You also are limited to two heads.  But compared to regular IDEX, you lose the extra motors, motor drivers, and design work, which is a win.

Q: What toolheads can I use with MadMax?

A: Anything compatible with the toolhead plate choices. See the [Getting Started](GETTING_STARTED.md) guide.

To attach to the docks, your toolhead needs to have the holes for the FHCSes already in place, or you can use a template to add those holes in, “in post”.

### Printable Space and Number of Heads
Q: How much print space do I lose?

A: It depends on the type of print and whether you make adjustments to enable a fixed Nudge mount.
The below assumes that the bed is close to the size of the printable XY space, and that we have a static-gantry printer or docks-ride-with-gantry flying-gantry printer.



* For single-extruder prints - assuming you detach the unused second head:
 * X
   * No loss, if your printer already has 3mm of X overtravel on one side.
   * 3mm X loss on one side, if no overtravel, but only at the front area by the dock.
 * Y
   * None, if you use a non-fixed Nudge mount (floating or indexed).
   * 6mm+ Y if you use a fixed Nudge mount and square bed; typically the front or back will be reserved for probing, and a bed shift may be needed.
 * Z
   * None, if you use a non-fixed Nudge mount.
   * Some, if you use a Nudge mount that requires the bed to be raised and you don’t already have Z overtravel available.
* For two-extruder prints
 * The lost space is typically the two front corners; for narrow printers like a V0, that front area becomes narrow, and usable only for prime lines.
 * X:
   * Depends on toolhead choice:
   * On each side - width of head + X-stick-out of screws (3mm) + clearance (1-2mm)
 * Y:
   * Y-dock-sliding-motion (~6mm) + Y-screw-stick-out-from-plate (4mm) + max Y depth of toolhead (varies)
 * Z
   * Same as single-extruder
Alternately, you can eliminate travel loss for two-extruder prints by:
* going wide (X widening equal to double the toolhead width in X, just like an IDEX)
* going deep (Y lengthening equal to the dock travel + screw stick-out + toolhead length in Y
* going tall (like a TapChanger/StealthChanger build, but only for flying-gantry printers)

Q: How many heads can I fit?

A: Depends on the printer of course, but also on available overtravel, as well as whether you want to do front or rear probing.  If doing front probing, you’ll need to reserve space for the probing motion, which would be the head width in X, plus the travel needed for Nudge (6mm+), plus a bit of clearance (1-2mm).

### Design Questions

Q: What unknowns remain in the design?

A: For full disclosure, we don’t know everything about it.  Early dev started in later 2023, but there are still some “how well does it work in practice?” questions.
* Whether the magnet hold is sufficient for superhigh accels and heavy toolheads, especially at elevated chamber temps.  So far, so good, even with crazy accels on Andrewmcgr's TMC4671-based Trident.
* Pull on the belts from attach/detach triggers viscoelastic hysteresis effects that may create errors within a print, over time.  Has not been quantified, but does not appear to be significant in prints.
* Whether Maxwell probing accuracy and Nudge alignment accuracy retains with higher chamber temps, and over time.
* IS effects, over a larger range of toolheads and printers.  Your before-and-after data is highly valuable here.
* Toolhead coupling wear.  So far, so good, especially with acetal.  PTFE shows visible wear, too quickly.  It's too soft.

### Why not < X >?

Q: Why no Boop here?

A: Boop’s great, but adds weight and force and design complexity.  We already have a Maxwell coupling.  Why not use it?  It will do triple-zero repeatability, despite being based on sliding friction.

Failing that, you can use your preferred low-force probing mechanism, whether Klicky-ish, Beacon, or other.

Higher-force mechanisms (Poke, Peck, Metal Peck) are not recommended yet, as you’re combining two springs at that point.

Q: Why not use the PrusaXL/Daksh latch mechanism for positive attachment?

A: It’s a great mechanism that uses rolling friction and has a solid mechanical lock.   It will scale better to heavier toolheads. But it also adds weight and a non-COTS part.
Magnets are, surprisingly, good enough here.  Overall simplicity and portability was a goal here.

Q: Why V0 support?

A: A V0 toolchanger is an affordable dev platform.  You can even just make the gantry to play with, maybe from spare parts, to learn and test the software side.

You don’t *need* to expand the frame, because you can easily detach a head and have something almost identical to a typical V0, just with an easier-to-maintain toolhead.  That’s a sweet V0.  It adds capabilities, in the same space.

Plus, you can expand the frame anyway, easily, as done with Tri-Zero plus.  A Plus-size V0 is a killer V0.  Multi material and more build space!  Just add frame extensions, large panels, and longer rails and belts.  It’s a small delta to a kit and you can use the shorter rails with T0.

But all that said - yeah, it’s not the best choice because of the inherent Y loss from the second head.  Larger just makes more sense here if you care about the usable workspace for two-extruder parts.

Q: Why aren’t there MiniSBs in use by default?  Can I reuse mine?

A: Simple - you can’t fit two MiniSBs (57mm width) in a normal V0 and have space for mechanical automatic alignment from a Nudge probe in the front.  Also, given that there are now many more choices that give extruder flexibility and easier maintenance, others are gaining traction.  OmniBrick, DragonBurner, and DragonBrick solve that.
Some notes about this:
* On a smaller build, a camera + Z probe per head would almost solve the space issue: 114 + 57 —> 171... but it’d be really tight unless you have extra overtravel from a Pandora X gantry.
* Z prefers the maintenance ease of a toolhead that has a detachable extruder, and loves that the PapLite can handle anything with high quality, in a tight package - especially abrasives (like CF-ABS), without killing the drive gear.
* OmniBrick and DragonBrick fit the toolhead board in front, which gives more usable Y travel.  Remember, when the active head is moving, it has to keep clear of the parked heads.  A deeper-in-Y head results in loss of usable Y here, and we’re already tight; the MiniSB does not leave space for a front toolhead.

Q: Why not add a fridge door?

A:
* Go ahead!  It makes everything easier.  You can then mount Nudge to the front extrusion and can fit a larger 130x130 MRW bed in place.
* If you do this, you may want to shift the docks forward slightly to make use of the extra travel.

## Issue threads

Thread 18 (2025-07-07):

Clarity in build instructions - some suggestions and questions

mossholderm, 2025-07-07:
Hi all!

I had some suggestions for the build documentation. Hopefully this will help other people when building the madmax system!

1. For the CAD drawings, consider having the different parts in different colors. It isn't really apparent from the illustration which parts go where.  For example, the printed parts in color "A", magnetic screws in color "b", normal screws in color "c", metal pins in color "d", plastic pins in color "e", and magnets in color "f".
2. Consider having a picture for each step of the assembly, with call outs to the specific part locations. I'm willing to give it a shot, but I have more questions :)
3. From the BOM, what is "250mm 2-position zip wire"? There isn't a link, and searching the term doesn't really return anything definitive. Not looking for an answer here, but rather something more descriptive in the BOM.
4. The M3 T-Nut for the "nut push tool" doesn't look like any of the M3 T-Nuts on Amazon... are these the MakerBeam XL T-nuts from the BOM? If so, consider naming the same way here.
5. Where do the "two middle-height pins" (plastic) go? Another case where a picture would do wonders (and if you can clear it up for my, I can provide one).

zruncho3d, 2025-07-07:
1,2: Thanks for the feedback.  I've tried to make the docs here much better than the usual "just the CAD" you see, but I don't want to commit to step-by-step pictures until we have more builds, because a change to the design would require redoing a lot of work, then.   Point taken on colors in CAD - that would certainly clear things up.

3: zip wire would be joined wires that can be unzipped. Example I use, 24 AWG silicone wire: I buy the 4-pos, and split it into 2x2 or 4x1 or 1x4 as needed: dhttps://www.aliexpress.us/item/2251832766791205.html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

4: yes, MBXL

5: if you look at the plate, they're in the middle.  Not the two top vertically-oriented pins for the top maxwell screw, but the plastic middle ones; the lower ones are on the bottom of the coupling and need to be metal.

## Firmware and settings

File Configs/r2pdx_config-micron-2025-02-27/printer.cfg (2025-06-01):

[include mainsail.cfg]
[include klipper-toolchanger/macros.cfg]
[include klipper-toolchanger/tool_detection.cfg]
[include klipper-toolchanger/toolchanger.cfg]
[include klipper-toolchanger/toolboard_0.cfg]
[include klipper-toolchanger/toolboard_1.cfg]
[include klipper-toolchanger/nudge_macros.cfg]
[include klipper-toolchanger/stealthburner_macros_tc.cfg]
[include timelapse.cfg]
[include priming.cfg]

[mcu]
serial: /dev/serial/by-id/usb-Klipper_stm32f446xx_530033000551313133353932-if00
restart_method: command

[mcu toolboard_0]
canbus_uuid: 3f46065d5747

[mcu toolboard_1]
canbus_uuid: 922ecbd4c103

#[mcu afc]
#canbus_uuid: 008ec7a804f8

[virtual_sdcard]
path: /home/micron/printer_data/gcodes
on_error_gcode: CANCEL_PRINT

[printer]
kinematics: corexy
max_velocity: 800
max_accel: 8000
max_z_velocity: 100
max_z_accel: 1000
square_corner_velocity: 5.0

[exclude_object]

[input_shaper]

[force_move]
enable_force_move: true

[respond]

[save_variables]
filename: ~/printer_data/config/klipper-toolchanger/offset_save_file.cfg

#####################################################################
#   X Stepper
#####################################################################

[stepper_x]
step_pin: PF9
dir_pin: PF10
enable_pin: !PG2
rotation_distance: 32
microsteps: 64
endstop_pin: toolboard_0: PB5
position_min: 0

position_endstop: 174
position_max: 174

homing_speed: 40
homing_retract_dist: 5

[tmc2209 stepper_x]
uart_pin: PF2
interpolate: false
run_current: 0.8
sense_resistor: 0.110

#####################################################################
#   Y Stepper
#####################################################################

[stepper_y]
step_pin: PC13
dir_pin: PF0
enable_pin: !PF1
rotation_distance: 32
microsteps: 64
endstop_pin: PG9
position_min: 0

position_endstop: 191
position_max: 191

homing_speed: 40
homing_retract_dist: 5

[tmc2209 stepper_y]
uart_pin: PE4
interpolate: false
run_current: 0.8
sense_resistor: 0.110

#####################################################################
#   Z Steppers
#####################################################################

[stepper_z]
step_pin: PF13
dir_pin: PF12
enable_pin: !PF14
rotation_distance: 40
gear_ratio: 9:1
microsteps: 32
endstop_pin: PG6
position_max: 250
position_min: -10
# position_endstop: 0
homing_speed: 10
second_homing_speed: 3
homing_retract_dist: 2

[tmc2209 stepper_z]
uart_pin: PC4
interpolate: False
run_current: 0.8
sense_resistor: 0.110

[stepper_z1]
step_pin: PG0
dir_pin: !PG1
enable_pin: !PF15
rotation_distance: 40
gear_ratio: 9:1
microsteps: 32

[tmc2209 stepper_z1]
uart_pin: PD11
interpolate: False
run_current: 0.8
sense_resistor: 0.110

[stepper_z2]
step_pin: PF11
dir_pin: PG3
enable_pin: !PG5
rotation_distance: 40
gear_ratio: 9:1
microsteps: 32

[tmc2209 stepper_z2]
uart_pin: PC6
interpolate: False
run_current: 0.8
sense_resistor: 0.110

[stepper_z3]
step_pin: PG4
dir_pin: !PC1
enable_pin: !PA0
rotation_distance: 40
gear_ratio: 9:1
microsteps: 32

[tmc2209 stepper_z3]
uart_pin: PC7
interpolate: False
run_current: 0.8
sense_resistor: 0.110

#####################################################################
#  Extruder PID settings, in here so we can save_config
#####################################################################

[extruder]
#control: pid
#pid_Kp: 36.965
#pid_Ki: 4.650
#pid_Kd: 73.468

[extruder1]
#control: pid
#pid_Kp: 36.965
#pid_Ki: 4.650
#pid_Kd: 73.468

#####################################################################
#   Fan Control
#####################################################################

[controller_fan power_supply_1]
pin: PA8
max_power: 0.5
cycle_time: 0.016
kick_start_time: 0.5
heater: heater_bed

[controller_fan power_supply_2]
pin: PE5
max_power: 0.5
cycle_time: 0.016
kick_start_time: 0.5
heater: heater_bed

[controller_fan mcu_fans_1]
pin: PD12
max_power: 0.5
cycle_time: 0.016
kick_start_time: 0.5
heater: heater_bed

[controller_fan mcu_fans_2]
pin: PD13
max_power: 0.5
cycle_time: 0.016
kick_start_time: 0.5
heater: heater_bed

[fan_generic bed_fan]
pin: PD14
cycle_time: 0.016
kick_start_time: 0.5

#####################################################################
#   Extra temperature sensors
#####################################################################

[temperature_sensor octopus]  # Also valid for stm32f042 mcus
sensor_type: temperature_mcu
sensor_mcu: mcu
min_temp: 0
max_temp: 80

[temperature_sensor raspberry_pi]
sensor_type: temperature_host
gcode_id: D
min_temp: 0
max_temp: 80

[temperature_sensor chamber]
sensor_type: Generic 3950
sensor_pin: PF4
min_temp: 0
max_temp: 80

#####################################################################
#   Bed Heater
#####################################################################

[heater_bed]
heater_pin: PA2
sensor_type: Generic 3950 
sensor_pin: PF3
pwm_cycle_time: 0.016
smooth_time: 3.0
max_power: 1.0
min_temp: 0
max_temp: 120
#control: pid
#pid_kp: 68.453
#pid_ki: 2.749
#pid_kd: 426.122

#####################################################################
#   Quad Gantry Level
#####################################################################

[quad_gantry_level]

##  Gantry Corners for Micron+ Build
gantry_corners:
  -60.2,-10.4
  244.1,234.5
##  Probe points for Micron+ Build
points:
  20,10
  20,160
  160,160
  160,10

speed: 200
horizontal_move_z: 5
retries: 5
retry_tolerance: 0.01
max_adjust: 10

#####################################################################
#   Bed Mesh
#####################################################################

[bed_mesh]
speed: 200
horizontal_move_z: 5
mesh_min: 10, 10
mesh_max: 170, 170
probe_count: 5,5
algorithm: bicubic
fade_start: 0.6
fade_end: 10.0
zero_reference_position: 90, 90

#####################################################################
#   Chamber LED
#####################################################################

[neopixel chamber_light]
## RGB light installed on bed mount
pin: PB0
chain_count: 29
color_order: GRB
initial_RED: 0.5
initial_GREEN: 0.5
initial_BLUE: 0.5

#####################################################################
#   Homing Overrides
#####################################################################

[gcode_macro homing_variables]
variable_safe_home_x: 13.3
variable_safe_home_y: 182.6
variable_safe_home_feed: 12000
gcode:

[homing_override]
axes: xyz
gcode:
    # Reset parameters.
    {% set X, Y, Z = False, False, False %}
    {% set hv = printer["gcode_macro homing_variables"] %}
    # Which axes have been requested for homing.
    {% if not 'X' in params
        and not 'Y' in params
        and not 'Z' in params %}
        {% set X, Y, Z = True, True, True %}
        # Raise the gantry 10mm.
        SET_KINEMATIC_POSITION Z=0
        G1 Z10 F2000
    {% else %}
        {% if 'X' in params %}
            {% set X = True %}
        {% endif %}
        {% if 'Y' in params %}
            {% set Y = True %}
        {% endif %}
        {% if 'Z' in params %}
            {% set Z = True %}
        {% endif %}
    {% endif %}
    {% if printer.toolchanger.status == "uninitialized" or printer.toolchanger.tool|int == -1 %}
        INITIALIZE_TOOLCHANGER
    {% endif %}

    {% if Y %}
      STATUS_HOMING
      G28 Y
    {% endif %}
    {% if X %}
      STATUS_HOMING
      G28 X
    {% endif %}
    {% if Z %}
      STATUS_HOMING
      # Move to z position switch location
      G0 X{hv.safe_home_x} Y{hv.safe_home_y} F{hv.safe_home_feed}
      G28 Z
      G0 Z10 F{hv.safe_home_feed}
    {% endif %}
    
    STATUS_READY

#####################################################################
#   Smart Homing
#####################################################################

[gcode_macro SMART_HOMING]
description: Homes and levels gantry if not already done.
gcode:
    {% set hv = printer["gcode_macro homing_variables"] %}
    {% if "xyz" not in printer.toolhead.homed_axes %}
        G28
    {% endif %}
    # Adjust the z_tilt if not done.
    {% if printer.z_tilt is defined %}
      {% if printer.z_tilt.applied == False %}
        Z_TILT_ADJUST
      {% else %}
        RESPOND MSG="Printer gantry already adjusted, skipping QGL."
      {% endif %}
    {% endif %}
    # Adjust QGL if not done
    {% if printer.quad_gantry_level is defined %}
      {% if printer.quad_gantry_level.applied == False %}
        QUAD_GANTRY_LEVEL
      {% else %}
        RESPOND MSG="Printer gantry already adjusted, skipping QGL."
      {% endif %}
    {% endif %}

#####################################################################
#   Print Start
#####################################################################

#print_start tool_0_start={first_layer_temperature[0]} tool_1_start={first_layer_temperature[1]} BED={first_layer_bed_temperature[0]} initial_tool={initial_tool} isT0={is_extruder_used[0]} isT1{is_extruder_used[1]}
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

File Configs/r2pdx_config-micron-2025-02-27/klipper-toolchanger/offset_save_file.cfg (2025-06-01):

[Variables]
current_tool = 0
nudge_position_x = 13.393
nudge_position_y = 183.291
nudge_position_z = 5.463
t0_offset_x = 0.0
t0_offset_y = 0.0
t0_offset_z = 0.0
t1_offset_x = 0.676
t1_offset_y = 0.766
t1_offset_z = 0.274

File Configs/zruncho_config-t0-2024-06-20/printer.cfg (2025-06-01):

[include mainsail.cfg]

# Derives from:
## Voron Design VORON2 250/300/350mm SKR 1.4 TMC2209 UART config

[mcu]
serial: /dev/serial/by-id/usb-Klipper_stm32f103xe_34FFD9054D50383535781543-if00

[mcu rpi]
serial: /tmp/klipper_host_mcu

[mcu z]
##	MCU for Z steppers
##	[Z in X] - Front Left
##	[Z1 in Y] - Rear Left
##	[Z2 in Z] - Rear Right
##	Obtain definition by "ls -l /dev/serial/by-id/" then unplug to verify
serial: /dev/serial/by-id/usb-Klipper_stm32f103xe_31FFD9054250373939640257-if00 
##--------------------------------------------------------------------

[include xy.cfg]
[include macros.cfg]
[include probe.cfg]
[include klipper-mini12864.cfg]

[include klipper-toolchanger/macros.cfg]
[include klipper-toolchanger/tool_detection.cfg]
[include klipper-toolchanger/toolchanger.cfg]
[include klipper-toolchanger/toolhead_0.cfg]
[include klipper-toolchanger/toolhead_1.cfg]
#[include klipper-toolchanger/toolhead_1_as_primary.cfg]
[include klipper-toolchanger/homing.cfg]

[include calibrate_offsets.cfg]

# Mellow ADXL board with CNC adapter:
#[include adxl345.cfg]

[auto_speed]

[force_move]
enable_force_move: true

[printer]
kinematics: corexy
# Reduced from 300
max_velocity: 200  
max_accel: 2000

max_z_velocity: 50
max_z_accel: 300  ; was 1000
square_corner_velocity: 5.0

# klipper-toolchanger expects this section to be present.
[bed_mesh]
speed: 120
horizontal_move_z: 5
mesh_min: 2, 75
mesh_max: 118, 110
probe_count: 3, 3

[input_shaper]
shaper_freq_x: 117.8
shaper_freq_y: 80.2
shaper_type_x: mzv
shaper_type_y: mzv

## Z MCU - In X Position
## Z0 Stepper - Front Left
[stepper_z]
step_pin: z:PB13
dir_pin: !z:PB12
enable_pin: !z:PB14
rotation_distance: 32
gear_ratio: 16:16
microsteps: 128
position_max: 119
endstop_pin: probe:z_virtual_endstop
position_min: -5
homing_speed: 8
second_homing_speed: 3
homing_retract_dist: 3

[tmc2209 stepper_z]
uart_pin: z:PC11
tx_pin: z:PC10
uart_address: 0
interpolate: true
run_current: 0.8
hold_current: 0.5
sense_resistor: 0.110
stealthchop_threshold: 500

## Z MCU - In Y Position
## Z1 Stepper - Rear Left
[stepper_z1]
step_pin: z:PB10
dir_pin: z:PB2
enable_pin: !z:PB11
rotation_distance: 32
gear_ratio: 16:16
microsteps: 128

[tmc2209 stepper_z1]
uart_pin: z:PC11
tx_pin: z:PC10
uart_address: 2
interpolate: true
run_current: 0.8
hold_current: 0.5
sense_resistor: 0.110
stealthchop_threshold: 500

## Z MCU - In E0 Position
## Z3 Stepper - Front Right
[stepper_z2]
step_pin: z:PB3
dir_pin: z:PB4
enable_pin: !z:PD2
rotation_distance: 32
gear_ratio: 16:16
microsteps: 128

[tmc2209 stepper_z2]
uart_pin: z:PC11
tx_pin: z:PC10
uart_address: 3
interpolate: true
run_current: 0.8
hold_current: 0.5
sense_resistor: 0.110
stealthchop_threshold: 500

[heater_bed]
pwm_cycle_time: 0.01

##	SSR Pin - Z board, Fan Pin
heater_pin: z:PC12
sensor_type: Generic 3950
sensor_pin: z:PC3
max_power: 1.0
min_temp: -200
max_temp: 120

control = pid
pid_kp = 55.226
pid_ki = 2.899
pid_kd = 263.013

[temperature_sensor chamber]
sensor_type: Generic 3950
# TH0 pin
sensor_pin: PA0
min_temp: -100
max_temp: 100

[heater_fan nevermore]
# FAN0
pin: z:PC6
heater: heater_bed
heater_temp: 50
fan_speed: 0.25

[heater_fan electronics_fan]
# FAN1
pin: z:PC7
heater: heater_bed
heater_temp: 50
fan_speed: 0.5

#*# <---------------------- SAVE_CONFIG ---------------------->
#*# DO NOT EDIT THIS BLOCK OR BELOW. The contents are auto-generated.
#*#
#*# [heater_bed]
#*# control = pid
#*# pid_kp = 55.226
#*# pid_ki = 2.899
#*# pid_kd = 263.013

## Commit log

2025-03-10 Initial beta commit; do not share without permission
    [Carriage_MGN12H.stl, Carriage_MGN12H_9mm.stl, Carriage_MGN9H.stl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]
2025-04-02 Add STLs
    [Belt Clip.stl, Dock Asembly.stl, Dock Bracket.stl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]
2025-04-02 Add STEP
    [MadMax 4 XOL v5.step]
2025-04-02 Make CAD directory, upload f3z
    [MadMax 4 XOL v5.step]
2025-04-02 Remove Belt Clip STL, it's not modified.
    [Belt Clip.stl]
2025-04-06 Add toolheads images
2025-04-06 Update carriage for printability
    [MadMax 4 XOL v11.step, MadMax 4 XOL v5.step, MadMaxCarriage.stl]
2025-04-06 Add print samples with use cases
2025-04-07 Doc updates, including parts plate
2025-04-07 Fix carriage STL orientation
    [MadMaxCarriage.stl]
2025-04-07 Fix case error
2025-05-11 Clarify virtual endstop homing
2025-05-25 Tighten words to get more picture size
2025-05-25 Tighten words to get more picture size, try 2
2025-05-25 Tighten words to get more picture size, try 3
2025-05-25 Tighten words to get more picture size, try 4
2025-05-27 Add BOM
2025-05-31 Link to BOM
2025-06-01 Rewrite configuration section and include helpful diagrams
    Add example configs
    [adxl345.cfg, archives.cfg, calibrate_offsets.cfg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]
2025-06-02 Add alternate A4T dock bracket
    [Alternate Bracket.step, Alternate Bracket.stl]
2025-06-03 Fix supports for bracket
    [Alternate Bracket.step, Alternate Bracket.stl]
2025-06-09 BOM: minor formatting fix (#11)
2025-06-09 Create Micron docks and Anthead duct modifications (#12)
    [ant_head_ducts-std.step, ant_head_ducts-std.stl]
2025-06-11 Add Trident Dock Arm STL
    [Dock Arm.stl]
2025-06-11 Add Trident Dock Arm STEP
    [Dock Arm.step]
2025-06-30 Add XOL plate for MGN9 (#15)
    Thanks!
    [MadMax_4_XOL_Plate_MGN9.step]
